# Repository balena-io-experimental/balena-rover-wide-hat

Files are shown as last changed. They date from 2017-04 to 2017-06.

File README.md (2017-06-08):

# Resin Rover Wide-HAT

This board is a full-fledged rover in a wide HAT form factor, which mean it covers an entire Raspberry Pi 3.

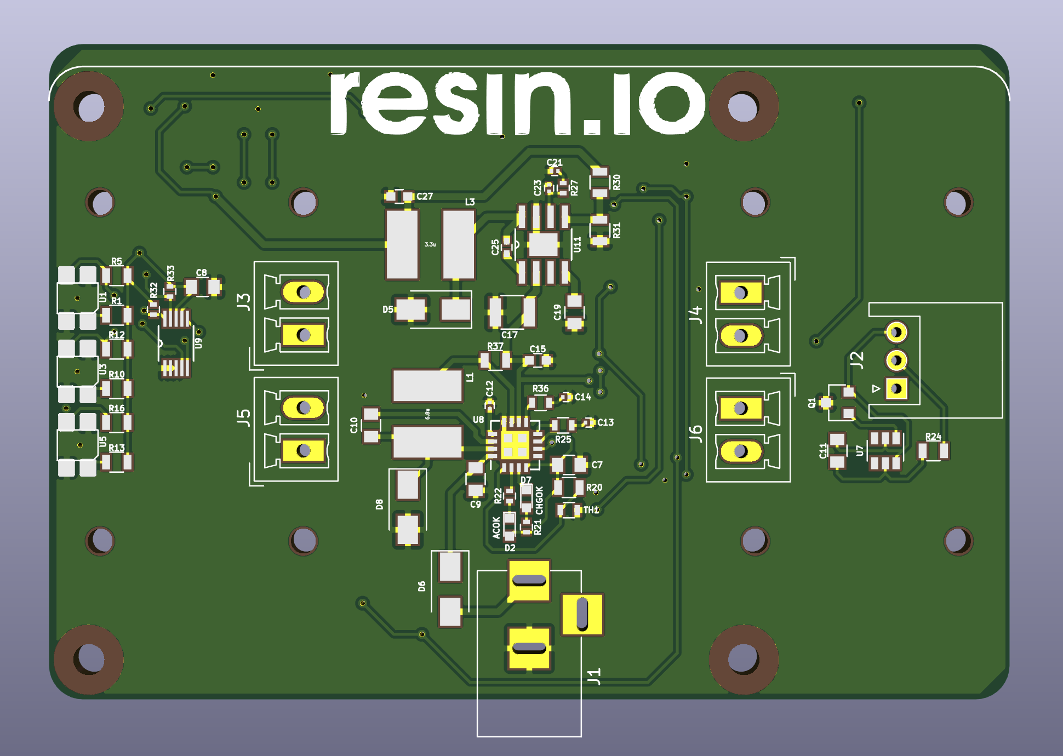
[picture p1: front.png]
front


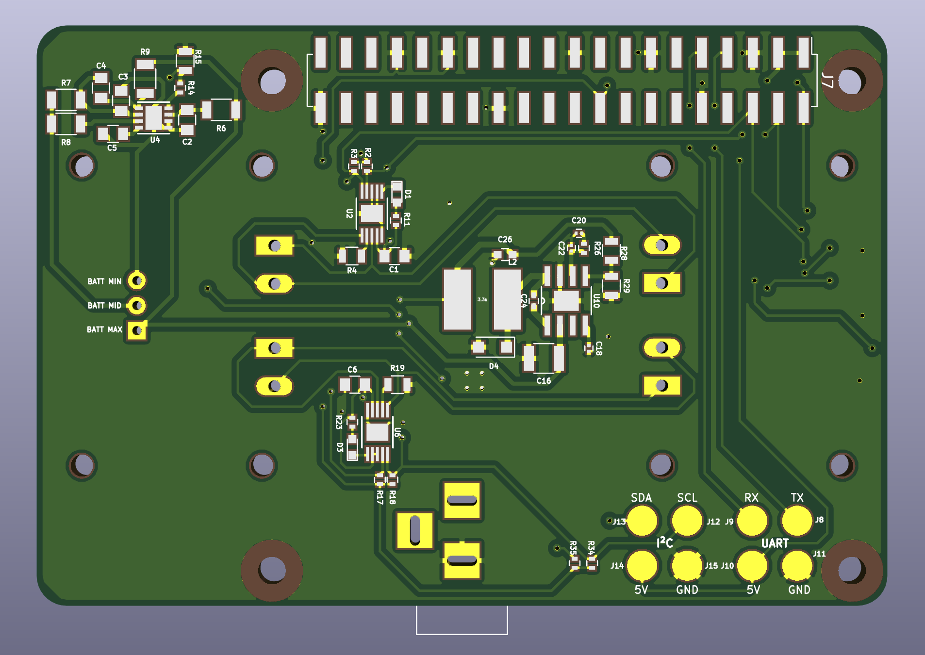
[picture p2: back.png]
back


The motors are driven by two [DRV8830](www.ti.com/product/drv8830) I²C motor controllers, one for the left wheels and the other for the right wheels. The slave I²C address for the left wheels driver are ``0xC0h`` and ``0xC1h``, for write and read respectively. As for the right wheels driver, they are ``0xD0h`` and ``0xD1h``, respectively.

Currently the maximum current for each motor is 500mA.

The line following circuit is made from three reflective sensors, which are read by an [ADC](http://www.ti.com/product/ADS1015) at address ``0x48h``. The left, center and right sensors are read at analog inputs ``AIN0``, ``AIN1`` and ``AIN2`` respectively.

It supports a 2-cell LiPo battery with an on-board charger which should be supplied through a DC barrel jack connector from 9V to 12V, at 1A.

The only manufacturing constrain of this board is that it needs 2oz or higher copper weight.

Besides the components listed on the BoM, the rest of the parts needed are:

* 4 x Micro Metal Gearmotor ([example](https://shop.pimoroni.com/products/micro-metal-gearmotor-extended-back-shaft))
* 4 x Micro Metal Gearmotor Bracket ([example](https://shop.pimoroni.com/products/pimoroni-gearmotor-bracket-pair))
* 4 x Wheels ([example](https://shop.pimoroni.com/products/pololu-wheel-32x7mm-pair))
* 1 x 2-cell LiPo battery with JST-XH connector ([example](https://hobbyking.com/en_us/turnigy-5000mah-2s-20c-lipo-pack.html))

Raspberry Pi mounting holes were taken from [here](https://github.com/xesscorp/RPi_Hat.pretty/blob/master/RPi_Hat_Mounting_Hole.kicad_mod) and inductor footprint from [here](https://github.com/Tinkerforge/kicad-libraries/blob/master/SRN6045.kicad_mod).

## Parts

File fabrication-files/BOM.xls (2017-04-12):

 | Bill of Materials (BOM)
Item # | Ref Des | Qty | Manufacturer | Mfg Part # | Description | Package | Type | Your Instructions
1 | C7 | 1 | Murata | GRM216R61E105KA12D | CAP CER 1UF 25V X5R 0805 | 805 | SMD
2 | C1 C6 | 2 | Murata | GRM219R61E106KA12D | CAP CER 10UF 25V X5R 0805 | 805 | SMD
3 | C9 | 1 | Murata | GRM21BR61E475KA12L | CAP CER 4.7UF 25V X5R 0805 | 805 | SMD
4 | C13 C14 | 2 | Murata | GRM033R71E222KA12D | CAP CER 2200PF 25V X7R 0201 | 201 | SMD
5 | C16 C17 | 2 | Murata | GRM32ER61C226KE20L | CAP CER 22UF 16V X5R 1210 | 1210 | SMD
6 | C18 | 1 | Kemet | C0201C270J3GACTU | CAP CER 27PF 25V C0G/NP0 0201 | 201 | SMD
7 | C19 | 1 | Samsung | CL21C300JBANNNC | CAP CER 30PF 50V C0G/NP0 0805 | 805 | SMD
8 | C20 | 1 | Murata | GRM033R71C102KA01D | CAP CER 1000PF 16V X7R 0201 | 201 | SMD
9 | C21 | 1 | Murata | GRM033R71C122KA01D | CAP CER 1200PF 16V X7R 0201 | 201 | SMD
10 | C22 C23 | 2 | Murata | GRM033R61A822KA01D | CAP CER 8200PF 10V X5R 0201 | 201 | SMD
11 | C24 C25 | 2 | Murata | GRM155R61A104KA01D | CAP CER 0.1UF 10V X5R 0402 | 402 | SMD
12 | C26 C27 C15 | 3 | TDK | C1608X5R1A226M080AC | CAP CER 22UF 10V X5R 0603 | 603 | SMD
13 | C11 C12 C2 C3 C4 C5 C8 C10 | 8 | Kemet | C0805C104K5RACTU | CAP CER 0.1UF 50V X7R 0805 | 805 | SMD
14 | D1 D3 | 2 | OSRAM | LR Q396-P1Q2-1 | LED RED DIFFUSED 0603 SMD | 603 | SMD
15 | D2 D7 | 2 | OSRAM | LG Q396-PS-35 | LED GREEN DIFFUSED 0603 SMD | 603 | SMD
16 | D4 | 1 | Fairchild | SS13FL | DIODE SCHOTTKY 30V 1A SOD123F | SOD-123F | SMD
17 | D5 | 1 | Toshiba | CMS06 | DIODE SCHOTTKY 30V 2A MFLAT | M-FLAT | SMD
18 | D6 D8 | 2 | Toshiba | CMS04(TE12L,Q,M) | DIODE SCHOTTKY 30V 5A MFLAT | M-FLAT | SMD
19 | J1 | 1 | CUI | PJ-002AH | CONN PWR JACK 2X5.5MM SOLDER | 3 pins | Through hole | Oval drill holes
20 | J2 | 1 | JST | S3B-XH-A | CONN HEADER XH SIDE 3POS 2.5MM | 3 pins | Through hole
21 | J3 J4 J5 J6 | 4 | Phoenix Contact | 1869363 | CONN TERM BLOCK 2POS 3.81MM | 2 pins | Through hole
22 | J7 | 1 | Kaweei | ADAFRUIT PRODUCT ID: 2714 | CONN HEADER 40POS SMT | 40 pins | SMD | https://www.adafruit.com/product/2714
23 | L1 | 1 | Bourns | SRN6045-6R8Y | FIXED IND 6.8UH 2.8A 47.3 MOHM | Custom | SMD
24 | L2 L3 | 2 | Bourns | SRN6045-3R3Y | FIXED IND 3.3UH 3.2A 30.2 MOHM | Custom | SMD
25 | Q1 | 1 | Nexperia | 2N7002 | MOSFET N-CH 60V 0.36A SOT-23 | SOT-23 | SMD
26 | R1 R10 R13 | 3 | Vishay Dale | CRCW0805100RKNEAIF | RES SMD 100 OHM 10% 1/8W 0805 | 805 | SMD
27 | R14 R17 R18 R2 R3 R32 R33 R34 R35 | 9 | Vishay Dale | CRCW04024K70JNED | RES SMD 4.7K OHM 5% 1/16W 0402 | 402 | SMD
28 | R12 R15 R16 R20 R24 R5 | 6 | Yageo | RC0805JR-0710KL | RES SMD 10K OHM 5% 1/8W 0805 | 805 | SMD
29 | R19 R4 | 2 | Panasonic | ERJ-S6SJR20V | RES SMD 0.2 OHM 5% 1/4W 0805 | 805 | SMD
30 | R11 R21 R22 R23 | 4 | Vishay Dale | CRCW04021K00JNEDHP | RES SMD 1K OHM 5% 1/5W 0402 | 402 | SMD
31 | R25 | 1 | Vishay Dale | CRCW06032K49FKEA | RES SMD 2.49K OHM 1% 1/10W 0603 | 603 | SMD
32 | R37 | 1 | Panasonic | ERJ-S6SJR20V | RES SMD 0.2 OHM 5% 1/4W 0805 | 805 | SMD
33 | R36 | 1 | Vishay Dale | CRCW0603750RFKEA | RES SMD 750 OHM 1% 1/4W 0603 | 603 | SMD
34 | R26 | 1 | Vishay Dale | CRCW040230K1FKED | RES SMD 30.1K OHM 1% 1/16W 0402 | 402 | SMD
35 | R27 | 1 | Vishay Dale | CRCW040226K7FKED | RES SMD 26.7K OHM 1% 1/16W 0402 | 402 | SMD
36 | R28 | 1 | Panasonic | ERA-6AEB103V | RES SMD 10K OHM 0.1% 1/8W 0805 | 805 | SMD
37 | R30 | 1 | Koa Speer | RN732ATTD1052B25 | RES SMD 10.5K OHM 0.1% 1/8W 0805 | 805 | SMD
38 | R29 | 1 | Panasonic | ERA-6AEB1541V | RES SMD 1.54K OHM 0.1% 1/8W 0805 | 805 | SMD
39 | R31 | 1 | Vishay Dale | TNPW08052K00BEEA | RES SMD 2K OHM 0.1% 1/8W 0805 | 805 | SMD
40 | R7 | 1 | Vishay Dale | CRCW1206240RJNEAHP | RES SMD 240 OHM 5% 3/4W 1206 | 1206 | SMD
41 | R6 R8 R9 | 3 | Vishay Dale | CRCW1206150RFKEAHP | RES SMD 150 OHM 1% 3/4W 1206 | 1206 | SMD
42 | TH1 | 1 | Murata | NCP18XH103J03RB | NTC THERMISTOR 10K OHM 5% 0603 | 603 | SMD
43 | U1 U3 U5 | 3 | Fairchild | QRE1113GR | SENSOR OPTO TRANS REFL SMD PHOTO | 4-SMD | SMD
44 | U10 U11 | 2 | Texas Instruments | TPS54332DDAR | IC REG BUCK ADJ 3.5A 8SOPWRPAD | 8-PowerSOIC | SMD
45 | U4 | 1 | Texas Instruments | BQ29209DRBR | IC VOLT PROT 2-CELL LI-ION 8SON | 8-VDFN | SMD
46 | U2 U6 | 2 | Texas Instruments | DRV8830DGQR | IC MOTOR DRIVER I2C 10MSOP | 10-MSOP | SMD
47 | U8 | 1 | Monolithic Power Systems | MP2610ER-LF-P | IC BATT CHRG LI-ION | 16-VQFN | SMD
48 | U9 | 1 | Texas Instruments | ADS1015IDGSR | IC ADC 12BIT I2C 3.3KSPS 10MSOP | 10-VSSOP | SMD
 |  | 94

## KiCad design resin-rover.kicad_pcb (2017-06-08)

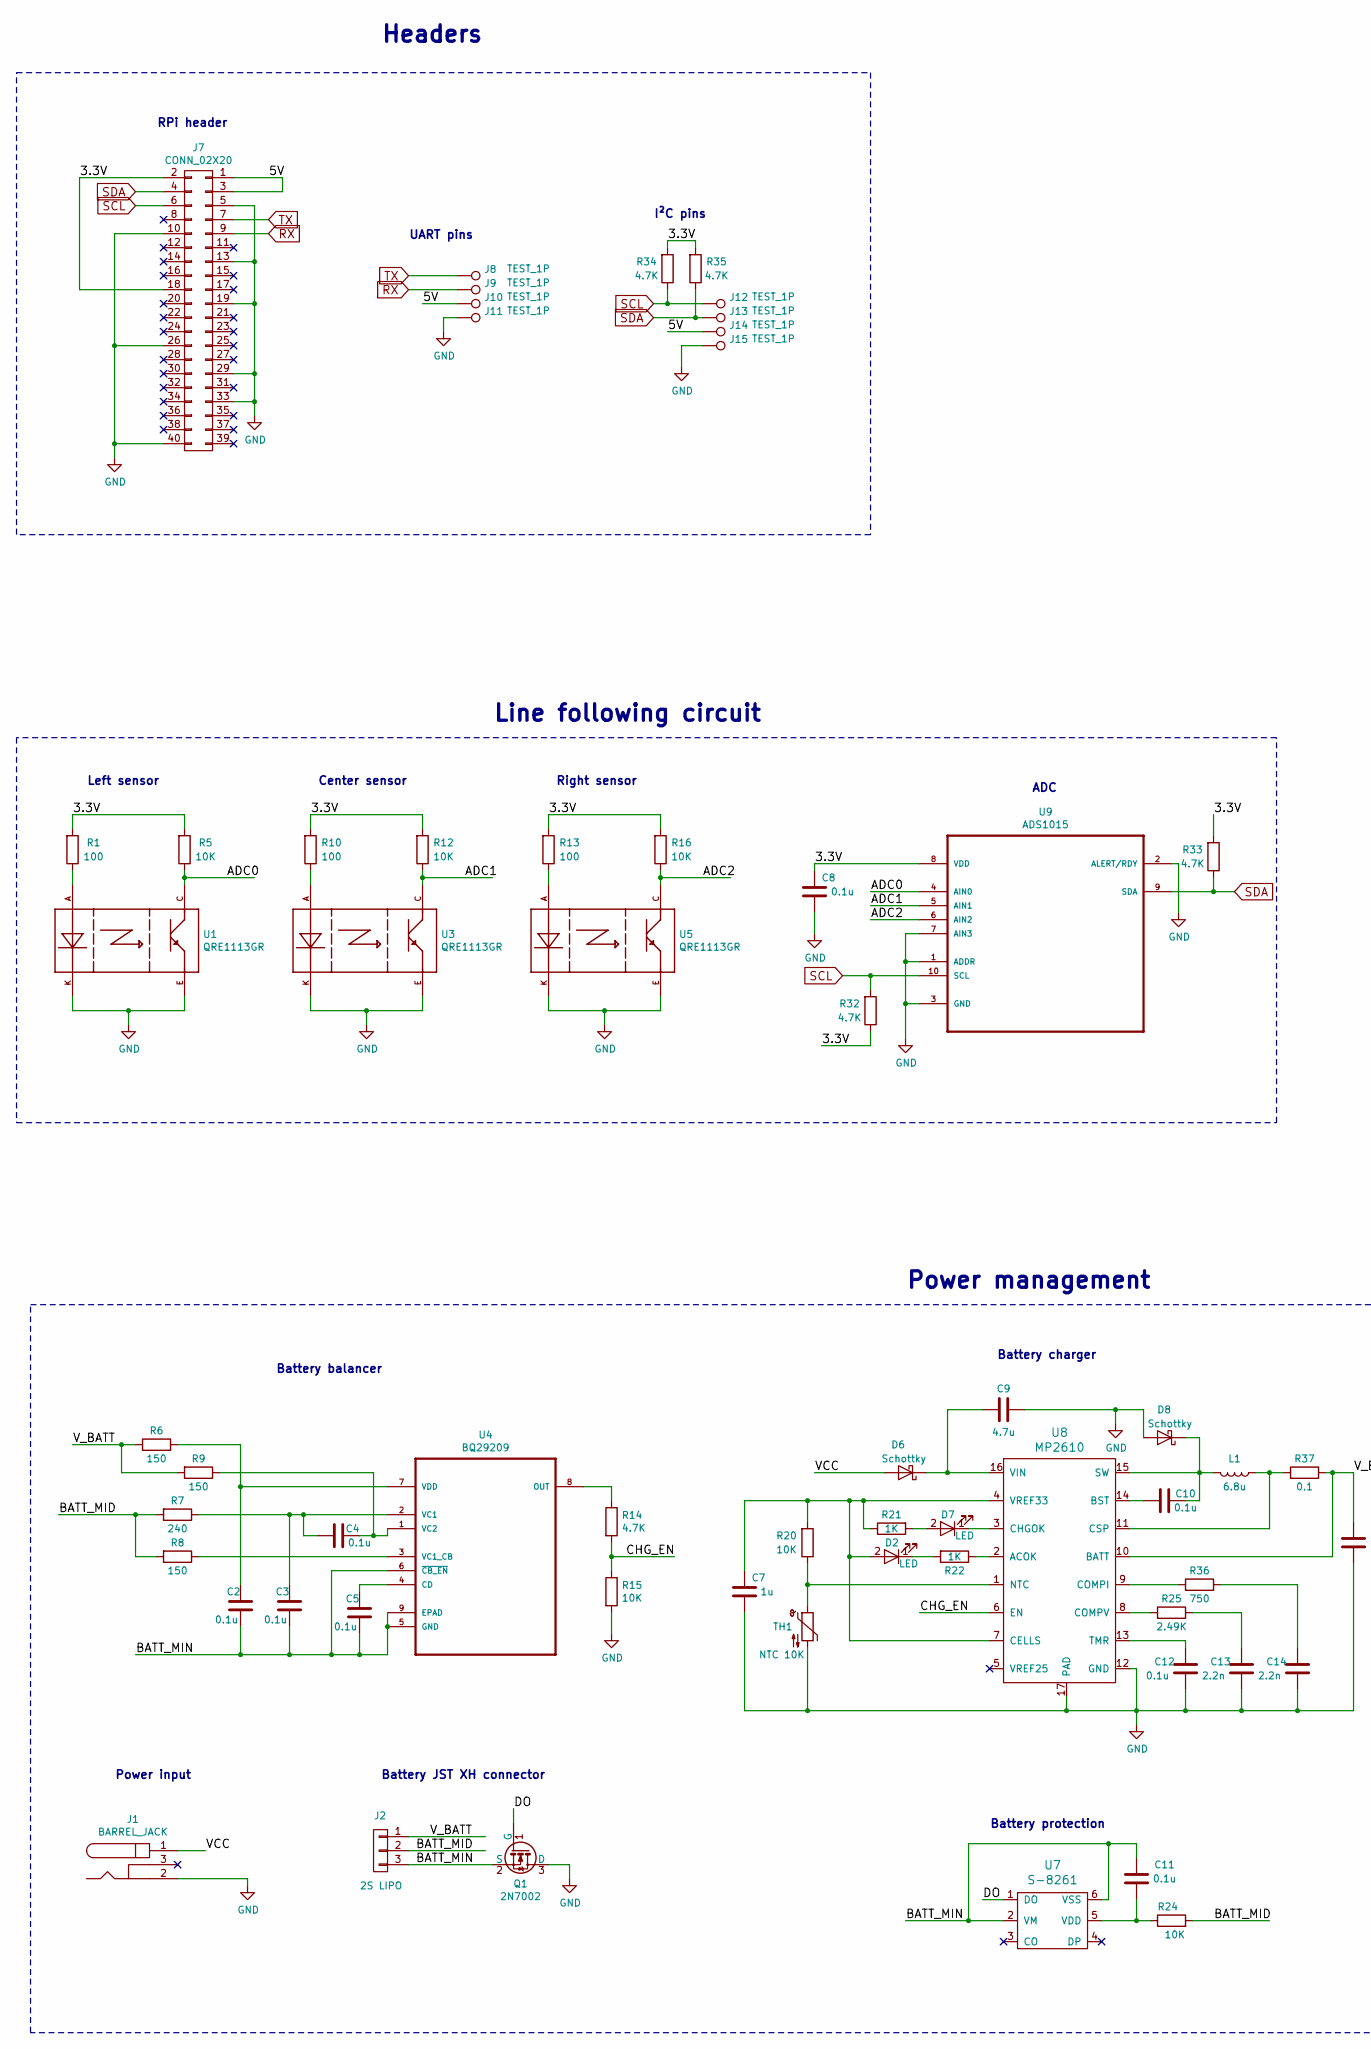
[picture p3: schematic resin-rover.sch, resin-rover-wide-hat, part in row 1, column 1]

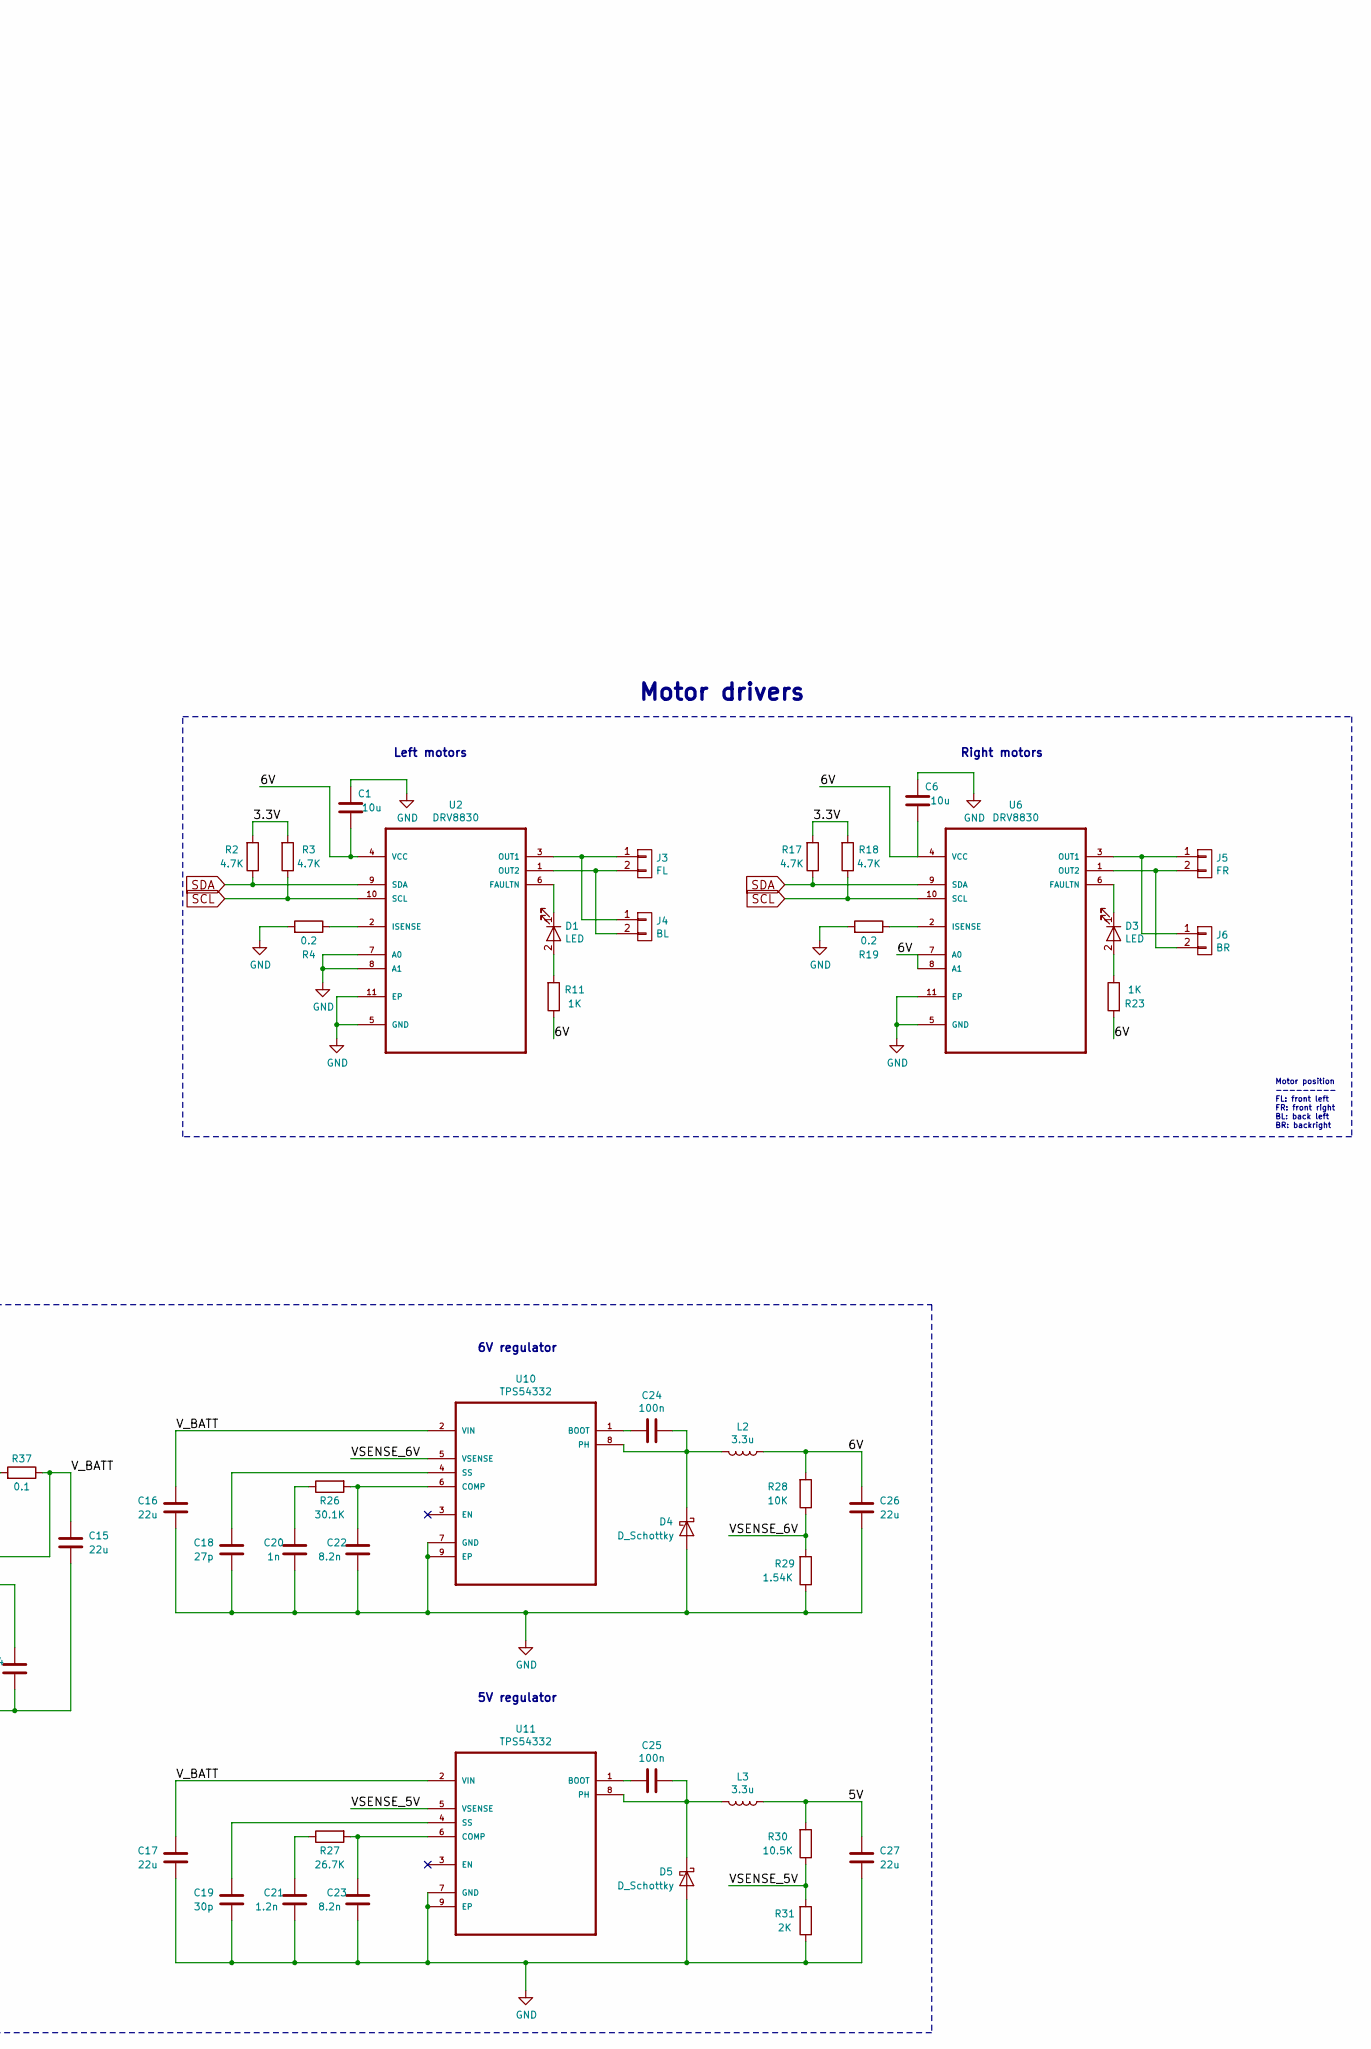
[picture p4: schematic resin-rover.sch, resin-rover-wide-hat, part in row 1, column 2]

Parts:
C1, C6: 10u; C_0805
C2, C3, C4, C5, C8, C10, C11: 0.1u; C_0805
C7: 1u; C_0805
C9: 4.7u; C_0805
C12: 0.1u; C_0201
C13, C14: 2.2n; C_0201
C15, C26, C27: 22u; C_0603
C16, C17: 22u; C_1210
C18: 27p; C_0201
C19: 30p; C_0805
C20: 1n; C_0201
C21: 1.2n; C_0201
C22, C23: 8.2n; C_0201
C24, C25: 100n; C_0402
D1, D2, D3, D7: LED; LED_0603
D4: D_Schottky; D_SOD-123F
D5: D_Schottky; D_SMA_Standard
D6, D8: Schottky; D_SMA_Standard
J1: BARREL_JACK
J2: 2S LIPO; JST_XH_S03B-XH-A_03x2.50mm_Angled
J3: FL; PhoenixContact_MCV-G_02x3.81mm_Vertical
J4: BL; PhoenixContact_MCV-G_02x3.81mm_Vertical
J5: FR; PhoenixContact_MCV-G_02x3.81mm_Vertical
J6: BR; PhoenixContact_MCV-G_02x3.81mm_Vertical
J7: CONN_02X20; Pin_Header_Straight_2x20_Pitch2.54mm_SMD
J8, J9, J10, J11, J12, J13, J14, J15: TEST_1P; Measurement_Point_Round-SMD-Pad_Big
L1: 6.8u; SRN6045
L2, L3: 3.3u; SRN6045
Q1: 2N7002; SOT-23
R1, R10, R13: 100; R_0805
R2, R3, R14, R17, R18, R32, R33, R34, R35: 4.7K; R_0402
R4, R19: 0.2; R_0805
R5, R12, R15, R16, R20, R24, R28: 10K; R_0805
R6, R8, R9: 150; R_1206
R7: 240; R_1206
R11, R21, R22, R23: 1K; R_0402
R25: 2.49K; R_0603
R26: 30.1K; R_0402
R27: 26.7K; R_0402
R29: 1.54K; R_0805
R30: 10.5K; R_0805
R31: 2K; R_0805
R36: 750; R_0603
R37: 0.1; R_0805
TH1: NTC 10K; R_0603
U1, U3, U5: QRE1113GR; 4LEADSMD
U2, U6: DRV8830; SOP65P640X110-15N
U4: BQ29209; SON65P315X315X100-9N
U7: S-8261; SOT-23-6
U8: MP2610; QFN-16-1EP_4x4mm_Pitch0.65mm
U9: ADS1015; SOP50P490X110-10N
U10, U11: TPS54332; SOIC127P600X170-9N

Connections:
/3.3V: C8.2, J7.2, J7.18, R1.2, R2.2, R3.2, R5.2, R10.2, R12.2, R13.2, R16.2, R17.2, R18.2, R32.1, R33.2, R34.2, R35.2, U9.8 (VDD)
/5V: C27.2, J7.1, J7.3, J10.1, J14.1, L3.1, R30.2
/6V: C1.1, C6.1, C26.2, L2.1, R11.1, R23.2, R28.2, U2.4 (VCC), U6.4 (VCC), U6.7 (A0), U6.8 (A1)
/ADC0: R5.1, U1.C, U9.4 (AIN0)
/ADC1: R12.1, U3.C, U9.5 (AIN1)
/ADC2: R16.1, U5.C, U9.6 (AIN2)
/BATT_MID: J2.2, R7.2, R8.2, R24.2
/BATT_MIN: C2.2, C3.1, C5.2, C11.2, J2.3, Q1.2 (S), U4.5 (GND), U4.6 (~CB_EN), U4.9 (EPAD), U7.2 (VM), U7.6 (VSS)
/CHG_EN: R14.2, R15.1, U8.6 (EN)
/DO: Q1.1 (G), U7.1 (DO)
/VCC: D6.2 (A), J1.1
/VSENSE_5V: R30.1, R31.2, U11.5 (VSENSE)
/VSENSE_6V: R28.1, R29.2, U10.5 (VSENSE)
/V_BATT: C15.2, C16.2, C17.2, J2.1, R6.1, R9.2, R37.1, U8.10 (BATT), U10.2 (VIN), U11.2 (VIN)
GND: C1.2, C6.2, C7.1, C8.1, C9.2, C12.1, C13.1, C14.1, C15.1, C16.1, C17.1, C18.1, C19.1, C20.1, C21.1, C22.1, C23.1, C26.1, C27.1, D4.2 (A), D5.2 (A), D8.2 (A), J1.2, J7.5, J7.10, J7.13, J7.19, J7.26, J7.29, J7.33, J7.40, J11.1, J15.1, Q1.3 (D), R4.2, R15.2, R19.2, R29.1, R31.1, TH1.2, U1.E, U1.K, U2.5 (GND), U2.7 (A0), U2.8 (A1), U2.11 (EP), U3.E, U3.K, U5.E, U5.K, U6.5 (GND), U6.11 (EP), U8.12 (GND), U8.17 (PAD), U9.1 (ADDR), U9.2 (ALERT/RDY), U9.3 (GND), U9.7 (AIN3), U10.7 (GND), U10.9 (EP), U11.7 (GND), U11.9 (EP)
unnamed: C2.1, R6.2, U4.7 (VDD)
unnamed: C3.2, C4.2, R7.1, U4.2 (VC1)
unnamed: C4.1, R9.1, U4.1 (VC2)
unnamed: C5.1, U4.4 (CD)
unnamed: C7.2, D2.2 (A), R20.2, R21.1, U8.4 (VREF33), U8.7 (CELLS)
unnamed: C9.1, D6.1 (K), U8.16 (VIN)
unnamed: C10.1, D8.1 (K), L1.2, U8.15 (SW)
unnamed: C10.2, U8.14 (BST)
unnamed: C11.1, R24.1, U7.5 (VDD)
unnamed: C12.2, U8.13 (TMR)
unnamed: C13.2, R25.1
unnamed: C14.2, R36.1
unnamed: C18.2, U10.4 (SS)
unnamed: C19.2, U11.4 (SS)
unnamed: C20.2, R26.1
unnamed: C21.2, R27.1
unnamed: C22.2, R26.2, U10.6 (COMP)
unnamed: C23.2, R27.2, U11.6 (COMP)
unnamed: C24.1, D4.1 (K), L2.2, U10.8 (PH)
unnamed: C24.2, U10.1 (BOOT)
unnamed: C25.1, D5.1 (K), L3.2, U11.8 (PH)
unnamed: C25.2, U11.1 (BOOT)
unnamed: D1.1 (K), U2.6 (FAULTN)
unnamed: D1.2 (A), R11.2
unnamed: D2.1 (K), R22.2
unnamed: D3.1 (K), U6.6 (FAULTN)
unnamed: D3.2 (A), R23.1
unnamed: D7.1 (K), U8.3 (CHGOK)
unnamed: D7.2 (A), R21.2
unnamed: J3.1, J4.1, U2.3 (OUT1)
unnamed: J3.2, J4.2, U2.1 (OUT2)
unnamed: J5.1, J6.1, U6.3 (OUT1)
unnamed: J5.2, J6.2, U6.1 (OUT2)
unnamed: L1.1, R37.2, U8.11 (CSP)
unnamed: R1.1, U1.A
unnamed: R4.1, U2.2 (ISENSE)
unnamed: R8.1, U4.3 (VC1_CB)
unnamed: R10.1, U3.A
unnamed: R13.1, U5.A
unnamed: R14.1, U4.8 (OUT)
unnamed: R19.1, U6.2 (ISENSE)
unnamed: R20.1, TH1.1, U8.1 (NTC)
unnamed: R22.1, U8.2 (ACOK)
unnamed: R25.2, U8.8 (COMPV)
unnamed: R36.2, U8.9 (COMPI)
RX: J7.9, J9.1
SCL: J7.6, J12.1, R3.1, R18.1, R32.2, R34.1, U2.10 (SCL), U6.10 (SCL), U9.10 (SCL)
SDA: J7.4, J13.1, R2.1, R17.1, R33.1, R35.1, U2.9 (SDA), U6.9 (SDA), U9.9 (SDA)
TX: J7.7, J8.1

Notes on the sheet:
Power input
Battery protection
Battery balancer
Battery JST XH connector
Battery charger
Power management
Motor drivers
Left motors
Right motors
Motor position --------- FL: front left FR: front right BL: back left BR: backright
6V regulator
5V regulator
UART pins
RPi header
I²C pins
Line following circuit
Center sensor
Left sensor
Right sensor
ADC
Headers

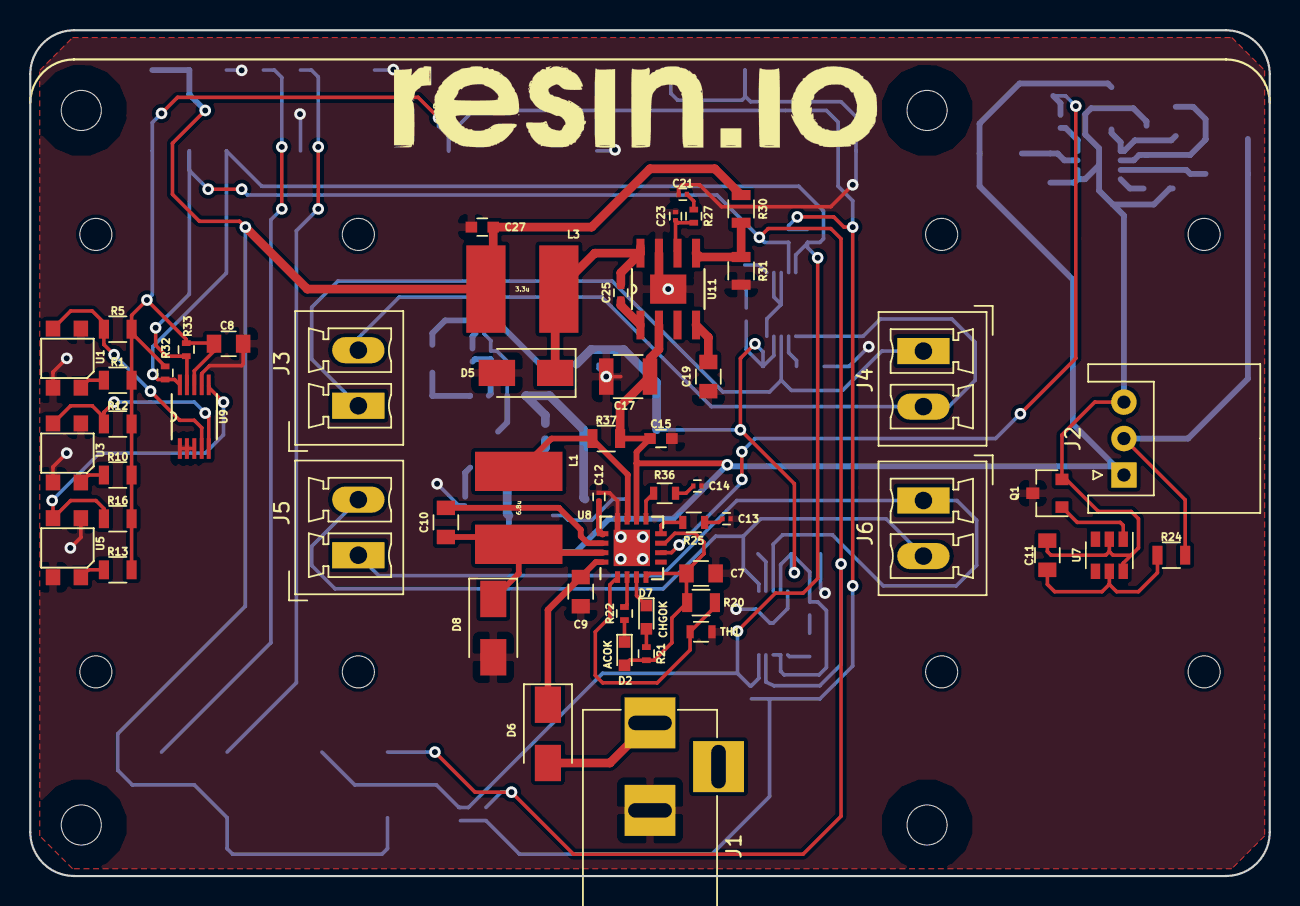
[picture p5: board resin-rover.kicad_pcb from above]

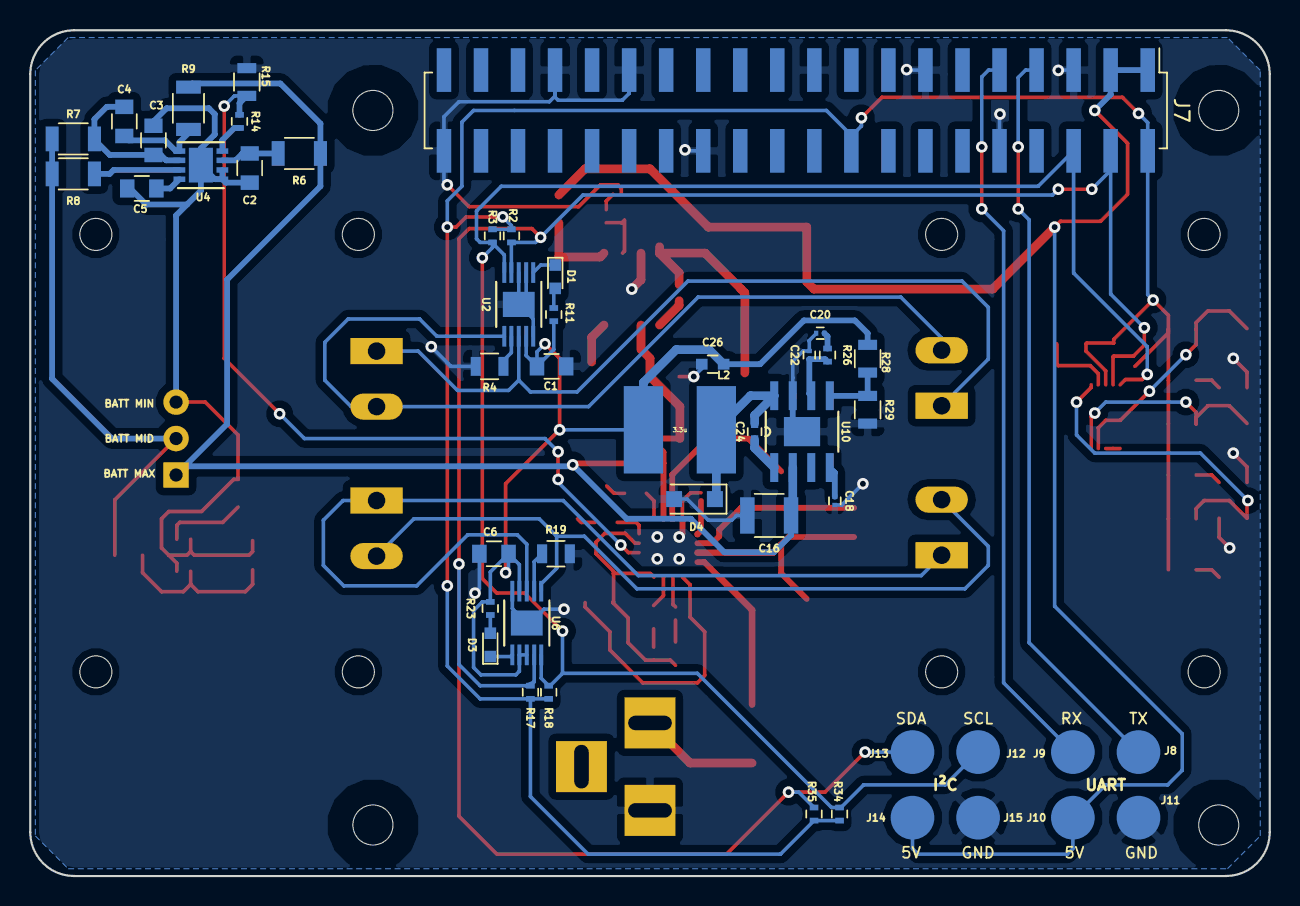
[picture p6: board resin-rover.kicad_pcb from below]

Board: 2 copper layers, 85.0 x 58.0 mm, 103 parts (48 on the bottom side), 64 nets.

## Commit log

2017-04-10 Add 5V and 6V voltage regulators
    [resin-rover.sch]
2017-04-10 Add line following circuit
    [resin-rover.sch]
2017-04-11 Add BOM and change battery charger to MP2610
    [BOM.xls, resin-rover.sch]
2017-04-12 Add layout and fabrication files
    [BOM.xls, resin-rover.kicad_pcb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]
2017-06-08 Update README and repo cleanup
    [resin-rover.kicad_pcb, resin-rover.sch]
